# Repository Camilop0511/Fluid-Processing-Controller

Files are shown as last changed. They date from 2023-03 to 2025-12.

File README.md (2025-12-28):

# Fluid Processing Controller 

## Overview 
This project implements a Fluid Processing Controller designed to simulate a small-scale industrial process, focusing on real-time monitoring, sequential control, and hardware–software integration. The system involves acquiring and controlling process variables related to fluids. It uses electronic components for fluid level and temperature measurements, including an MPX2010 pressure sensor for precise liquid level detection and an LM35DZ temperature sensor for accurate temperature monitoring.

The system features two storage tanks and a processing tank, managed by two water pumps and a heating resistor. It has both a physical control panel and a web-based interface for control. An ATmega8515 serves as the main controller, facilitating bidirectional communication with a Raspberry Pi. This setup allows users to input parameters and monitor the process through a web page hosted by the Raspberry Pi. 

Operationally, the system functions sequentially, ensuring meticulous control over each stage of fluid processing. This includes tasks such as filling, heating, and final delivery of the processed fluid.

## Repository Structure
- `src/`: Final version of the code.
- `test/`: Contains development history.
  - `microcontroller/`: Experimental and development code with test folders for various functionalities.
    - `actuators/`: Test code related to actuators.
    - `pwm/`: Test code for Pulse Width Modulation.
    - `sensors/`: Test code for sensors.
    - `sequential_control/`: Sequential control tests.
    - `serial_communication/`: Code test for serial communication between the microcontroller and Raspberry Pi.
  - `web_server/`: Development history of the web server code.
- `docs/`: Documentation files such as circuit designs, PCB designs, PCB illustrations, and a technical manual.

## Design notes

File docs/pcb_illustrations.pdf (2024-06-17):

243-698-DW Computer Network Project | 1

# 243-698-DW Computer Network Project

# PCB Illustrations

# Camilo Loaiza

1835111

# Nick Markou

# 28 April 2023

## Table of Contents

## 1. Main PCB Design

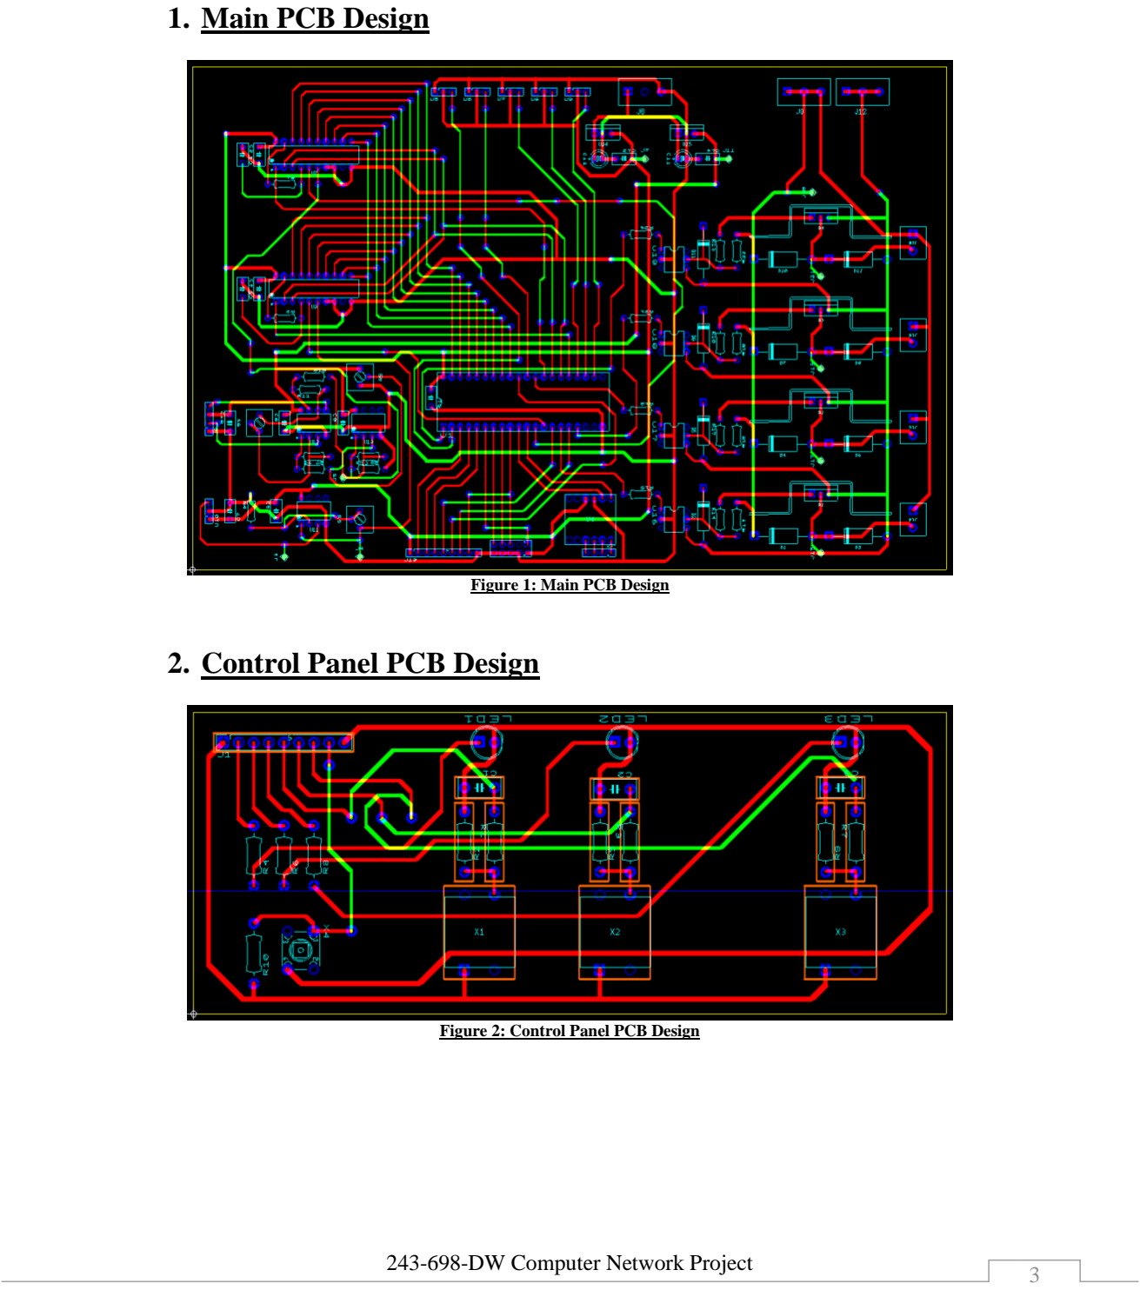
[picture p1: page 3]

Figure 1: Main PCB Design

## 2. Control Panel PCB Design

Figure 2: Control Panel PCB Design

## 3. Main PCB Layout

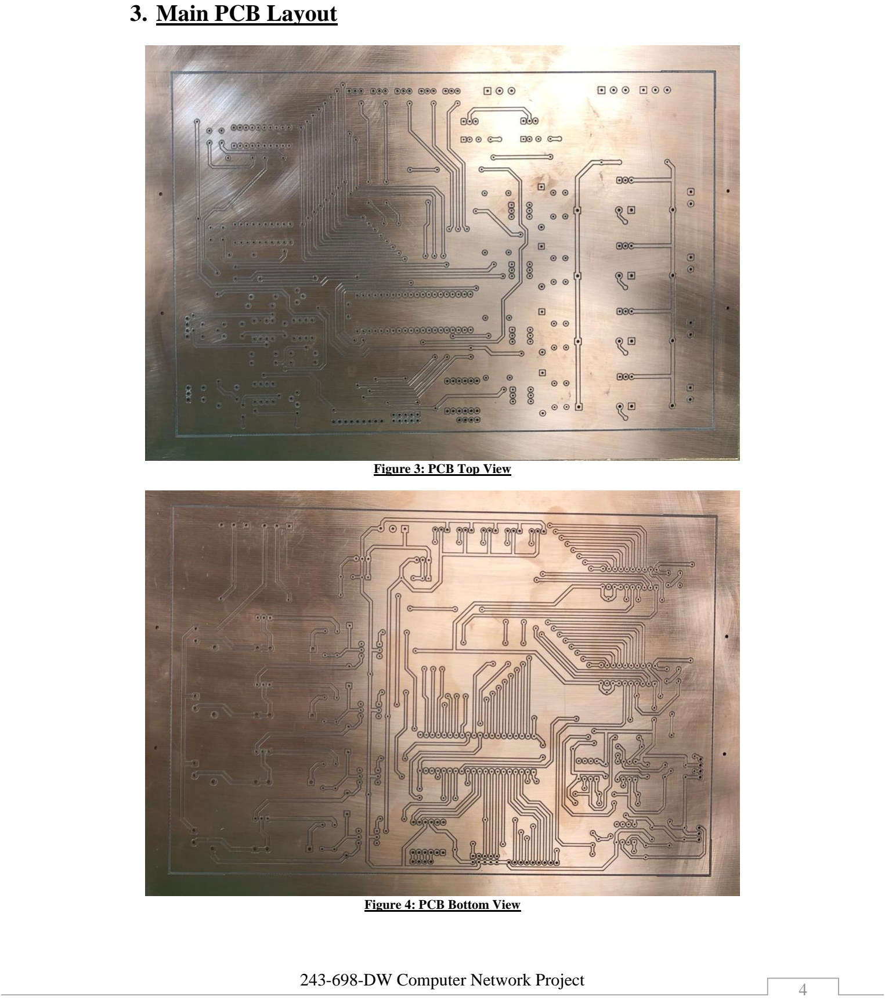
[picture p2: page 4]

Figure 3: PCB Top View

Figure 4: PCB Bottom View

## 4. Main PCB Vias Soldering

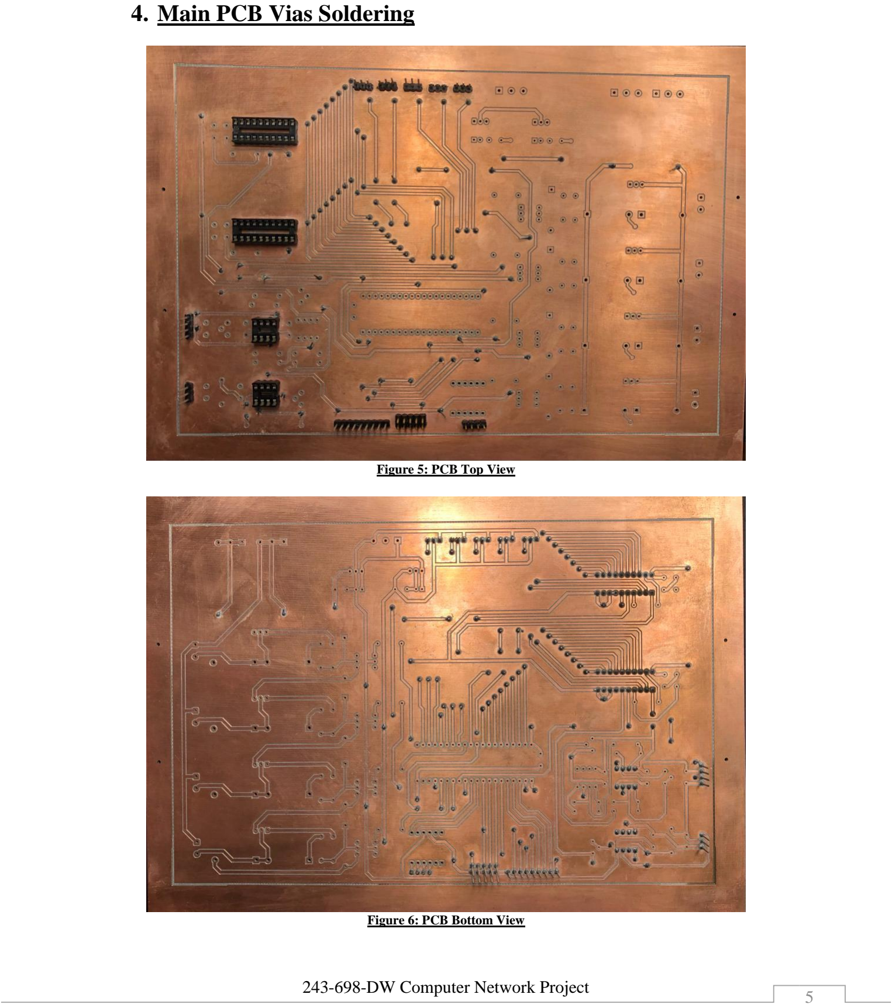
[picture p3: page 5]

Figure 5: PCB Top View

Figure 6: PCB Bottom View

## 5. Main PCB Soldering

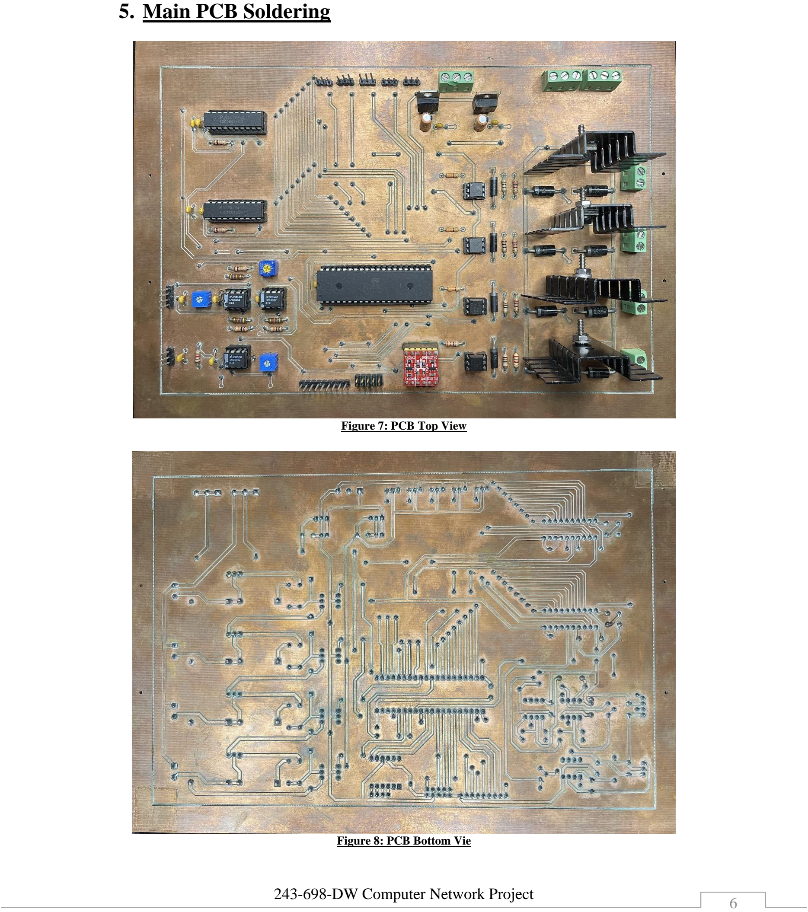
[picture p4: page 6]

Figure 7: PCB Top View

Figure 8: PCB Bottom Vie

## 6. Control Panel PCB Layout

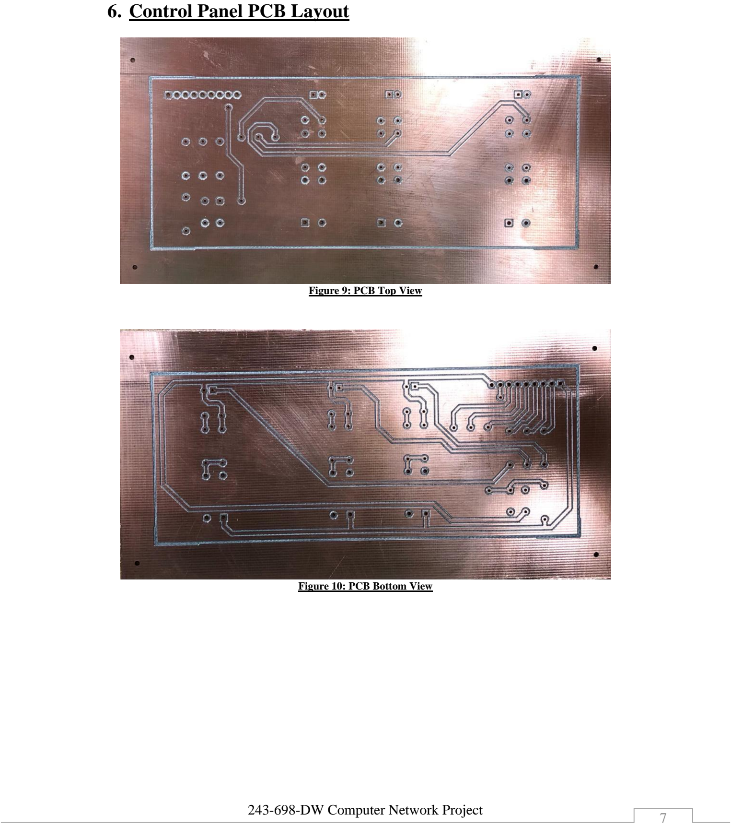
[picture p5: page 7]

Figure 9: PCB Top View

Figure 10: PCB Bottom View

## 7. Control Panel PCB Soldering

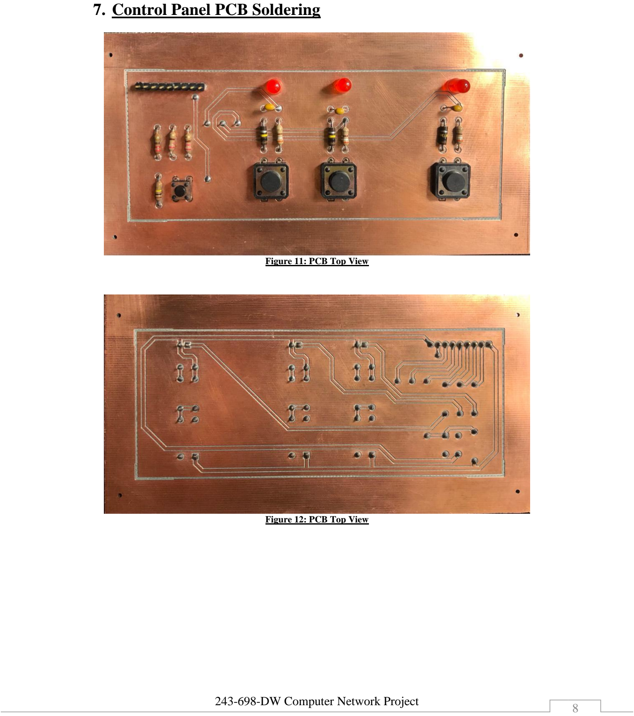
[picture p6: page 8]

Figure 11: PCB Top View

Figure 12: PCB Top View

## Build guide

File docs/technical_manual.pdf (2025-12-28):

## Table of Contents

## User Guide

## 1.0 Introduction

The resulting product of this project is a fluid processing controller that emulates a small-scale industrial process. It involves the acquisition and control of process variables with fluids using basic components for fluid level and temperature measurement such as pressure and temperature sensors. The system includes two liquid storages, a processing tank, and both physical and virtual control panels. Additionally, two water pumps are used to control the level in the processing tank coming from the storage tanks, a heating resistor is used to warm the water to the temperature that the user sets and an electro valve is utilized to serve the liquid when the process is finished. The genesis of this project is my interest in the food manufacturing industry and my desire to eventually have my own food processing business.

## 2.0 Setup and Operation

To properly configure and operate this product, it is necessary to connect both 12V and 24V power supplies to the PCB, as well as the temperature and pressure sensors and all actuators to their corresponding headers on the PCB. The Raspberry Pi must be powered on and its serial ports connected to the PCB, while also ensuring it has internet connectivity. To begin the process, the user should navigate to the Raspberry Pi's IP address, which can vary depending on the network's DHCP settings, and access the form page at /fluids_project/web_server/form.html. For example,
if the | Raspberry | Pi's | IP | address | is | 10.0.0.83, | the | user | should | browse | to
http://10.0.0.83:8080/fluids_project/web_server/form.html. On the form page, the user can enter their desired settings for the process, taking note of the restrictions and limits set for the parameters to optimize the system. Once the user has submitted the form, they can start, stop, and monitor variables such as temperature, processing tank volume, the state of start, stop and serve, as well as the current step of the process being executed. These are the different steps of the system and their meaning:
- Step 0: Microcontroller is waiting for serial values from Raspberry Pi.
- Step 1: The values sent from the Raspberry Pi are transferred to process variables.
- Step 2: Water Pump 1 is started.
- Step 3: Water Pump 1 is stopped.
- Step 4: Water Pump 2 is started.
- Step 5: Water Pump 2 is stopped.
- Step 6: Heating resistance is started.
- Step 7: Heating resistance is stopped.
- Step 8: Cooldown counter is executed.
- Step 9: Liquid can be served (electro-valve is opened).
- Step 10: Electro-valve is closed.

## 3.0 Specifications

Parameter | Minimum | Maximum | Unit
Input Voltage (Control circuit) | | 5
circuit) | | 24 | V Input Voltage (Power
Storage Tank Volume | | 1300 | ml
Water Pumps Voltage | 6.3 | 16.8 | V
Water Pumps Current | 0.27 | 0.83 | I
Water Pumps Power | 1.7 | 14 | W
Temperature in Processing Tank | 10 | 60
Temperature | 23 | 30 | °C Heated Liquid
Heating Resistor Voltage | 4.65 | 22.9 | V
Heating Resistor Current | 0.18 | 0.82 | I
Heating Resistor Power | 0.84 | 18.78 | W

## Technical Guide

## 4.0 System Diagram

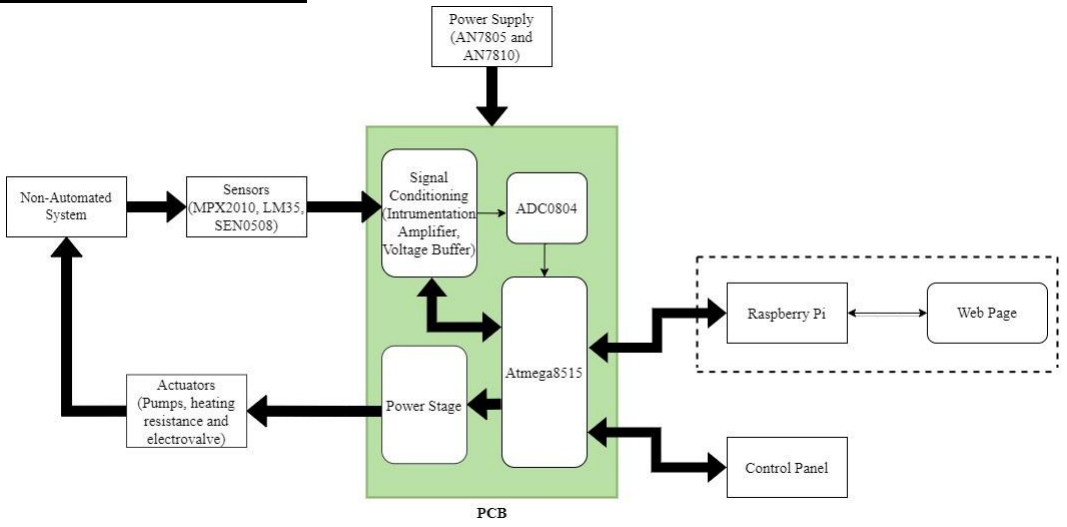
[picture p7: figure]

## 5.0 System Description

- Sensor Module:
- Pressure Sensor: The purpose of the MPX2010 pressure is to provide precise and reliable detection of the liquid level in the processing tank. This sensor works by measuring the pressure difference between its two ports, one exposed to the atmosphere and the other one exposed to the liquid in the tank, which changes the electrical resistance of the sensor as the liquid level changes. The intended operation is to ensure that the liquid level remains within the intended optimal ranges, while enabling accurate monitoring of the processing operation.
- Temperature Sensor: The purpose of the LM35DZ waterproof temperature sensor is to accurately measure and monitor the temperature of the liquid in the processing tank, and convert it into the corresponding electrical signal. The sensor’s output is linear, and proportional to the temperature in Celsius, with a scale factor of 10mV/ °C, which allows accurate and reliable temperature monitoring, and ensures that the processing tank operates within the desired temperature range.
- Capacitive Sensors: This module is designed to detect liquid level in the tanks using SEN0506 capacitive sensors. The purpose of this module is to determine whether the liquid level in the storage tanks is high or low, while in the processing tank, it will detect only the high level. The capacitive sensor used in the processing tank is as used as a redundancy method, since it works alongside the pressure sensor guaranteeing that the high liquid level in the processing tank is always detected and providing an extra layer of protection.
- Signal Conditioning Module:
- MPX2010 Signal Conditioning: The purpose of the signal conditioning module is to prepare the voltage signal obtained by the MPX2010 pressure sensor for use with the Analog-to-Digital converter. To achieve this, two LMC6062 OP-AMPs are connected to the sensor to server as an instrumentation amplifier. The instrumentation amplifier allows to filter out any noise present in the signal, adjust the offset, and adjust the gain before the signal is connected to the A/D converter. The intended operation is to ensure that the signal is optimized for the best possible measurement accuracy, and to minimize signal distortion.
- LM35 Signal Conditioning: The signal conditioning module for the LM35DZ temperature sensor prepares the analog signal for conversion into digital form by the ADC. Its purpose is to ensure accurate temperature readings by amplifying the signal, performing calibration, and linearization. By incorporating a gain of 5, this module enhances the signal’s sensitivity for better resolution and sensitivity. This module plays an important role to maintain the quality and consistency of the processing tank operation.
- ADC0804 Module: The purpose of the ADC0804 module is to convert the amplified analog voltage signal obtained from the instrumentation amplifier into digital format that can be read and processed by the Atmega8515 microcontroller. In addition to the pressure sensor’s ADC, another ADC0804 integrated circuit has been added to handle the analogto-digital conversion of the LM35DZ temperature sensor. The purpose of this module is to convert the voltage signal from the LM35DZ temperature sensor, which has already been amplified by the signal conditioning module, and the liquid level in the processing tank into digital data that can be processed by the microcontroller, providing accurate and reliable temperature and liquid level data for monitoring the processing tank operation. This module’s intended operation is to sample and convert the analog temperature signals and liquid level into digital data when indicated by the program.
- Power Supply Module: The power supply module comprises two regulated power supplies. The first is a 12V DC plug power supply adaptor that serves as the input to an LM7810 regulator, which supplies a stable 10V to the instrumentation amplifier. The same 12VDC plug also serves as the input to an LM7805 regulator, which provides a reliable 5V supply for the microcontroller, ADC, LM35 temperature sensor, and its signal conditioning module, a voltage buffer based on an operational amplifier. Additionally, a DC 24V 10A Power Supply Adapter Transformer Regulated Switch is utilized to power the actuators, which include the two water pumps, heating resistance, and electro valve. The power supply module not only provides the necessary voltage to operate all modules but also ensures the separation of the control and power sections of the circuit for enhanced safety. This separation is important given that the control section operates with 5V while the power section requires 24V.
- Power Stage Module: The power stage module is composed of four circuits, each dedicated to one of the four high-power actuators, all powered by 24V. The purpose of this module is to control the actuators’ power supply safely and efficiently using lower-power signals from the Atmega8515 microcontroller. To achieve this, optocouplers are used to isolate the high-voltage actuators from the low-voltage microcontroller, preventing voltage spikes and protecting the microcontroller, and allowing safe and efficient control of the power supply. The MOSFETs act as electronic switches that regulate the current flow to the actuators. The operation of the chopper circuit is synchronized with the microcontroller's PWM output signal, which serves as the input to the optocoupler and regulates the gate voltage of the MOSFETs. The chopper circuits use this switching mechanism to efficiently regulate the actuators' power supply while ensuring their safe operation and providing reliable control of the actuators.
- Actuators Module:
- Water Pumps: The purpose of the two water pumps is to transfer liquid from the storage tanks to the processing tank through pipelines. This transfer process is accomplished by regulating the speed of the water pumps through the chopper circuit, which is controlled by the Atmega8515 microcontroller's PWM signal. The intended operation of the water pumps is to accurately adjust their speed according to the signal received from the power stage module ensuring a precise liquid transfer.
- Heating Resistance: The heating resistance is responsible for raising the temperature of the processing tank’s liquid to a programmed value by converting electrical energy into thermal energy. The Atmega8515 microcontroller sends a PWM signal to the power stage module, which then controls the power delivered to the heating resistance. Overall, the intended operation of the heating resistance is to provide precise control of the liquid temperature through the microcontroller’s PWM signal and the power stage module.
- Electro valve: The electro valve serves as a security feature that prevents liquid from being served until the entire process is complete, and the user-defined cooling time has elapsed. The microcontroller controls the electro valve, allowing it to operate in two states: ON or OFF. If the conditions are not met, the electro valve remains OFF. The electro valve is connected to a regular port on the microcontroller since it only has two states, and also passes through the power stage module. Overall, the intended operation of the electro valve is to provide an added layer of safety and control to the processing tank’s liquid flow.
- The Atmega8515 Module: This module serves multiple purposes in the system. First, it is responsible for processing digital data obtained from the ADC0804 module, more specifically from the pressure and temperature sensors, which are passed through the signal conditioning and ADC modules. Additionally, This module also controls the actuators with the help of three PWMs which are configured on the microcontroller: two 16-bit PWMs which serve the two water pumps, and one 8-bit PWM that controls the heating resistance. The signals are sent to the power stage module, which then controls the actuators. Another of its responsibilities is the sequential control of the system. The sequential control involves a series of steps that must be followed to complete the processed, as long as all the necessary conditions are met. If any of the conditions in the step is not met, the process will not proceed to the next step. This sequential process is comprised of 11 steps:
- Step 1: The microcontroller waits for the process values from the Raspberry Pi, as well as the start signal.
- Step 2: The serial communication variables are transferred to the process variables.
- Step 3: Water pump 1 is started with the user-defined value.
- Step 4: Water pump 1 is stopped.
- Step 5: Water pump 2 is started with the user-defined value. o Step 6: Water pump 2 is stopped. o Step 7: The heating resistance is started with the user-defined value.
- Step 8: The heating resistance is stopped. o Step 9: The cooldown time counter is executed. o Step 10: Liquid is served after the serve signal is sent by user (electro-valve is opened). o Step 11: Electro-valve is closed after the pressure sensor detects that the water level is low.

The control sequence is dependent on meeting the necessary conditions and status of the start and stop signals. If the user sends a stop signal on the web server or physical control panel, the process will stop until a start signal is sent. The process then restarts from the step where it was stopped. Additionally, the process checks the water level of the storage tanks. If an empty tank is detected, or an error with the storage tank sensors is identified, the process will also stop.

The microcontroller is also responsible for the two-way serial communication with the Raspberry Pi. It reads two bytes sent by the Raspberry Pi to obtain the initial user-defined process values, where the first byte corresponds to a command identifying the type of data being sent, and the second byte is the data value. The same principle is applied when sending data from the microcontroller to the Raspberry Pi. The data values sent include the step, temperature, volume, start signal state, stop signal state, serve signal state and cooldown counter state.

- Raspberry Pi: The Raspberry Pi module serves two main purposes, which are hosting the web page, and communicating with the Atmega8515 microcontroller.
- Web Page: The web page is hosted using Apache 2 to provide a web server that allows direct interaction with the user. The main page, called form.html, prompts the user for multiple parameters that define the system’s behaviour, including the percentage of liquid from each tank, the speed of the water pumps, the desired temperature, the power percentage for the heating resistors, and the desired cooldown time before serving the liquid. The data from this page is then submitted to the formresults.php file, which comprises HTML, PHP, and JavaScript code. This page handles all the backend server process that is needed to effectively communicate with the Atmega8515 microcontroller.
- Logic Level Converter: This module facilitates the communication between the Atmega8515 microcontroller and the Raspberry Pi. This is achieved by converting the different voltage signals between the 3.3V logic level of the Raspberry Pi and the 5V logic level of the Atmega8515.
- Control Panel: The control panel module serves as a physical redundancy element for the buttons on the web page, enabling control over the system’s sequential steps by sending start, stop, and serve signals, just like the web page buttons. The control panel has the same functionality as the web page buttons but it offers added flexibility. In case of a web crash, unavailable internet connection, or failure to send data, the control panel allows for continued control over the system, enabling it to be stopped if necessary, and started without needing to use the web page. Additionally, the control panel includes three LEDs:
start, stop, and serve, which indicate the current status of the industrial process.
- PCB: The purpose of the PCB (Printed Circuit Board) is to provide a reliable connection for the multiple electronic components, including the microcontroller, ADCs, sensors, MOSFETs, actuators, and all other devices. The main PCB is divided into two parts: the control section on the left, which is comprised of the microcontroller and low-power devices, and the power section on the right, which is composed of the 24V-powered devices that provide control over the actuators. These two sections are separated by optocouplers that provide both electrical and visual isolation. The second PCB is the control panel which comprises the buttons and LEDs, and it is connected to main PCB using headers and wires.
- Non-automated Module: This module consists of various components that are part of the system but do not belong to the electrical circuitry such as the structure, the liquid storage tanks, the processing tank, and pipelines. One port of the MPX2010 pressure sensor is connected to a tube that is taped to the bottom of the processing tank to measure the pressure level of the liquid in the tank. ¼ inch vinyl tubing is being used to measure the pressure in the processing tank. The processing tank, along with two 4L storage tanks and pipelines, are also included in this module. The water pumps are connected to the storage tanks and the processing tank via 1/2 inch vinyl tubing, while the processing tank is connected to the electro valve using 3/8 inch vinyl tubing Additionally, manual valves were added to the processing tank to optimize the liquid’s flow and to act as redundancy components.

## 6.0 Circuit Description

- System’s Circuit

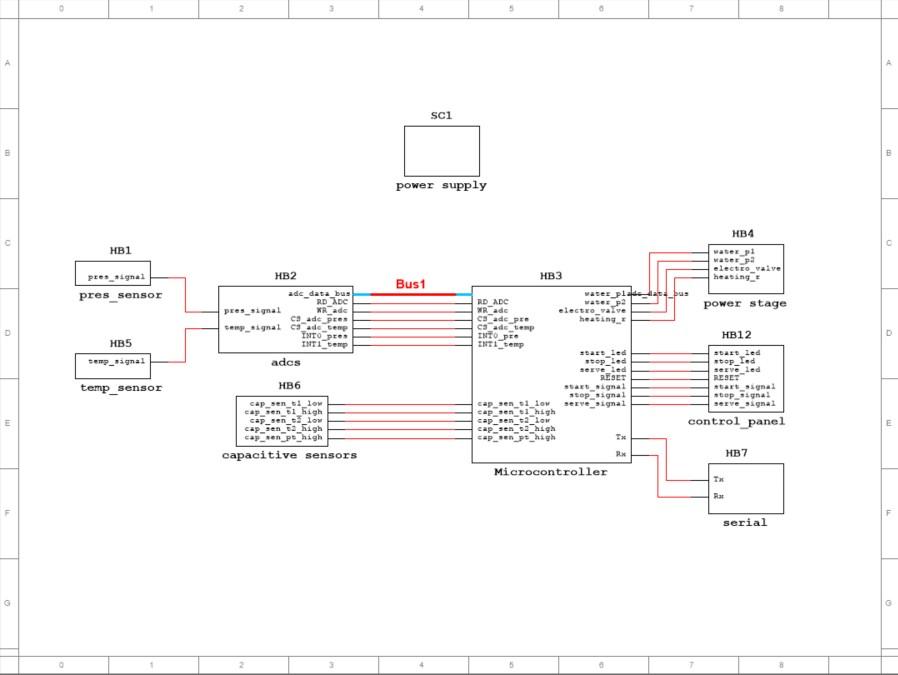
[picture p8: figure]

- Microcontroller: The control panel is connected to the microcontroller using regular ports configured as input for the start and serve signals, and as output for the LED signals. However, the stop button is connected to INT2 since it is a signal that requires immediate execution in the code and cannot be executed using the polling method. The logic level converter is connected to the Rx and Tx pins on the ATmega8515 which are part of the USART interface. The ADCs are connected to the address port, the control signals are connected to regular ports, and the ADC interrupts are connected to the interrupts on the microcontroller. The actuators are connected to the PWM pins, except for the electro-valve which is using a regular port.

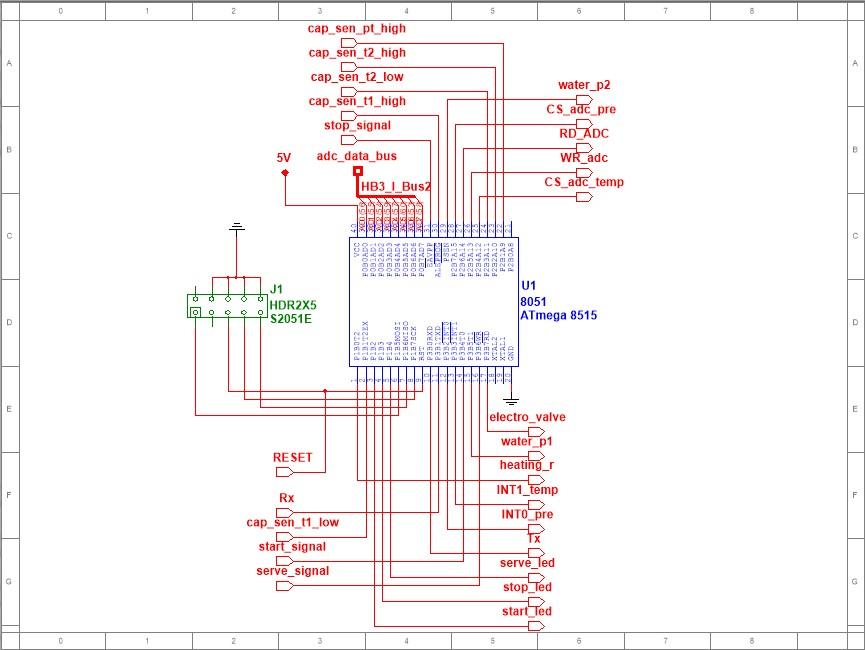
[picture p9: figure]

- ADCs: The data buses of both ADCs are connected to the same Port A of the Atmega8515 microcontroller, enabling the microcontroller to read data from each ADC. The write (/WR) and read (/RD) signals of both ADCs are also connected to the same /RD and /WR pins of the microcontroller, allowing the microcontroller to have control over their operation. The Chip Select (/CS) signal of each ADC is connected to different ports on the microcontroller, enabling the microcontroller to select which ADC to communicate with and read data from. The two ADCs are configured to run as interrupt-driven, meaning that when an ADC completes a conversion, it generates an interrupt signal on its INT pin which are connected to the microcontroller’s INT0 and INT1 external interrupts. The temperature and pressure sensors’ signals are connected to the inputs of the two ADCs, after passing through the signal conditional circuits, which are converted into digital values.

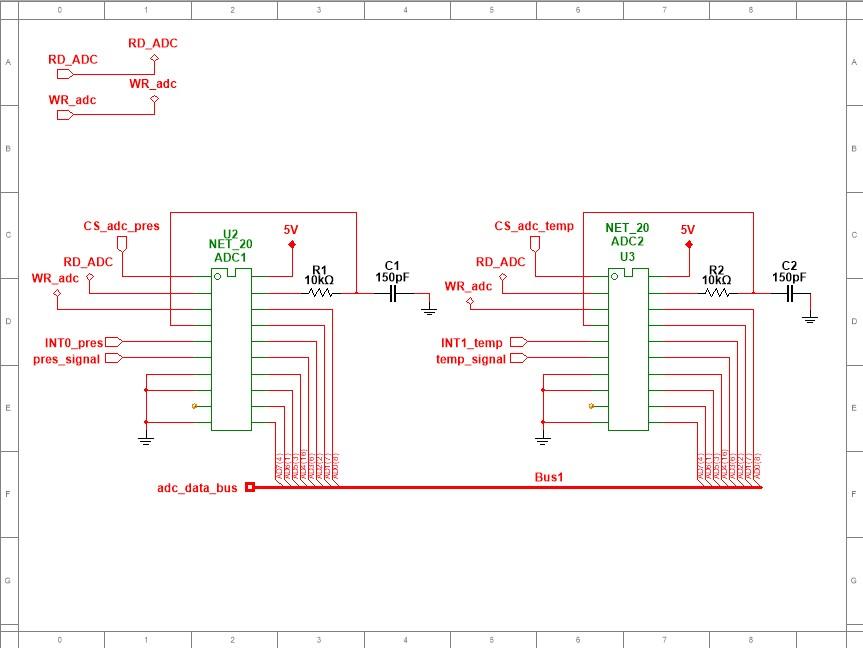
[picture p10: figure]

- Serial/Logic Level Converter: The logic converter is divided into two parts: the upper part connects to the Rx and Tx pins of the microcontroller and is also connected to is 5V VCC and ground, while the bottom part connects directly to the Rx and Tx pins of the Raspberry Pi, and to 3.3V and ground. This configuration ensures that the signals are properly converted between the two different voltage levels (5V and 3.3V) facilitating the exchange of data between the AVR microcontroller and the Raspberry Pi.

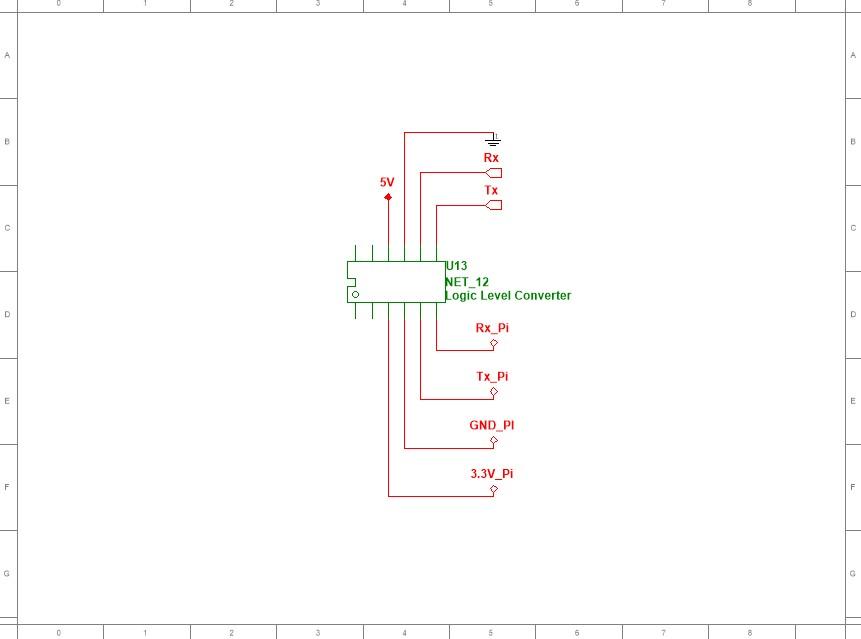
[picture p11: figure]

- Capacitive Sensors

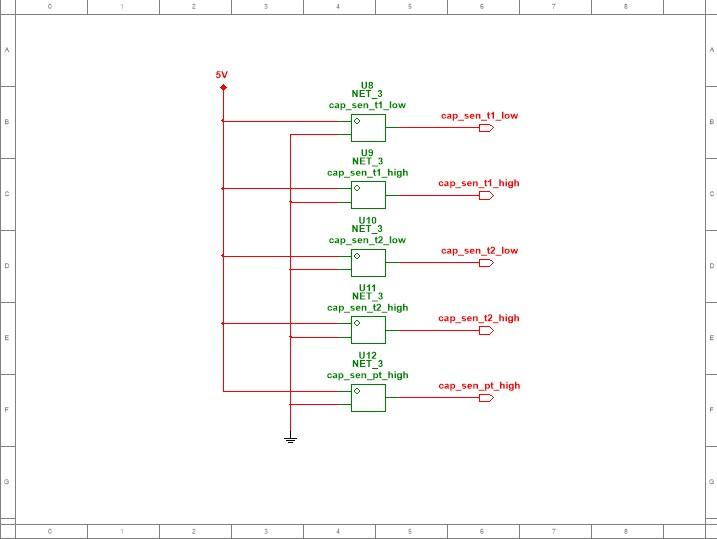
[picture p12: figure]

- Power Stage: The power stage circuit is designed as a chopper circuit. The PWM signal from the microcontroller is connected to the internal LED of the optocoupler. The ground of this LED is the same as the control section of the system. The transistor inside the optocoupler is connected such that the emitter is connected to the ground of the power section and the collector is connected to a resistor that goes to VCC (24V). A 1N5349 Zener diode connected between these two pins to act as a 12V voltage regulator to protect the MOSFET. The gate of the MOSFET is connected to the collector of the internal transistor of the optocoupler. Two 1n5401 diodes are connected to the MOSFET, one in parallel with the MOSFET having the cathode of the diode to the drain of the MOSFET and the anode to the source, and the other going from the drain to VCC in parallel with the load. These diodes protect the MOSFET and load from damage by preventing current from flowing back to them.

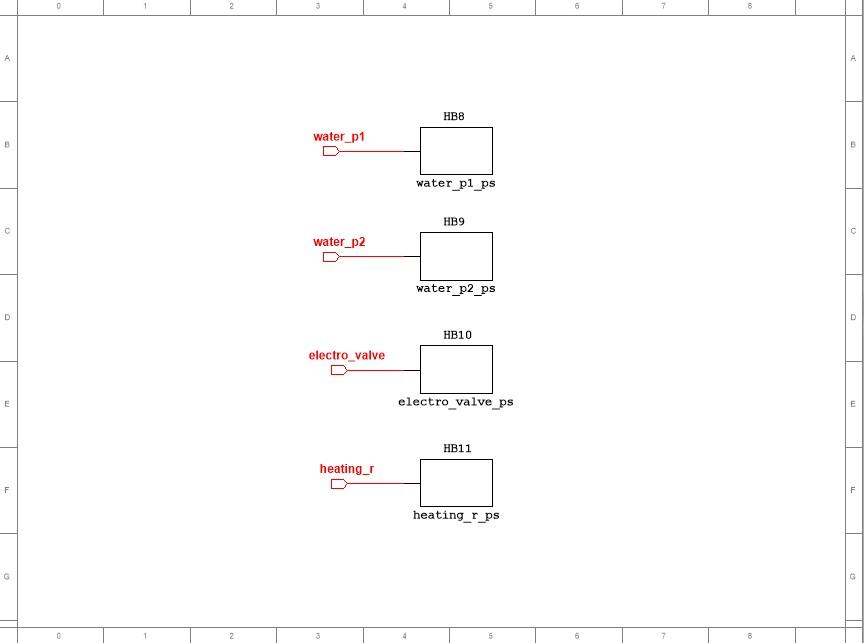
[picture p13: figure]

- Water Pump 1 Power Stage:

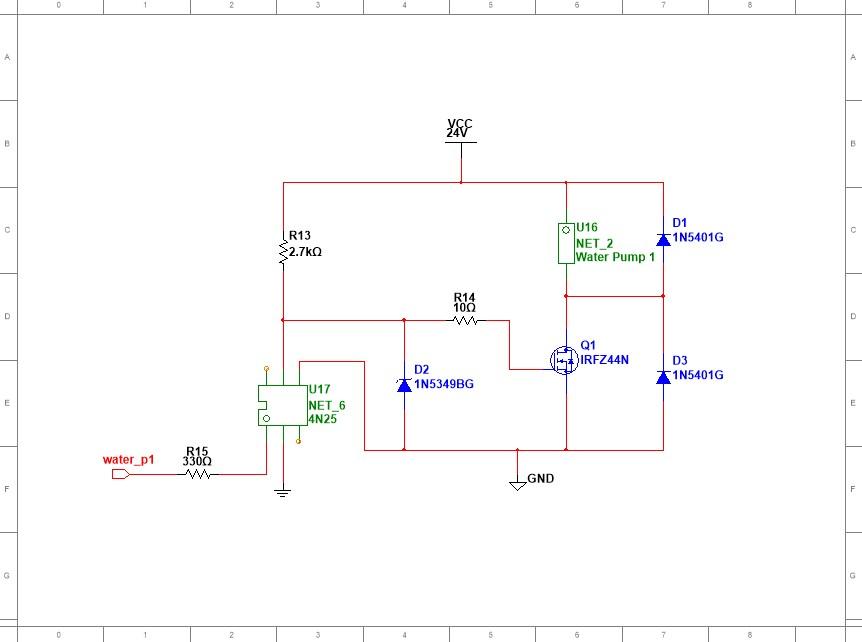
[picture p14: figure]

- Temperature Sensor: The LM35DZ signal conditioning circuit conditions the output of the LM35DZ sensor using an operational amplifier voltage buffer configuration. The noninverting input of the LMC6062 op-amp is connected to the output of the LM35DZ sensor, while the inverting input is connected to a 1k ohms resistor that is grounded. The loopback resistors of the circuit is a 5k ohm potentiometer that allows the gain of the circuit to be adjusted. This circuit has a gain of 5, meaning that if the output of the temperature sensor if 0.25V, the output of the circuit will be 1.25V.

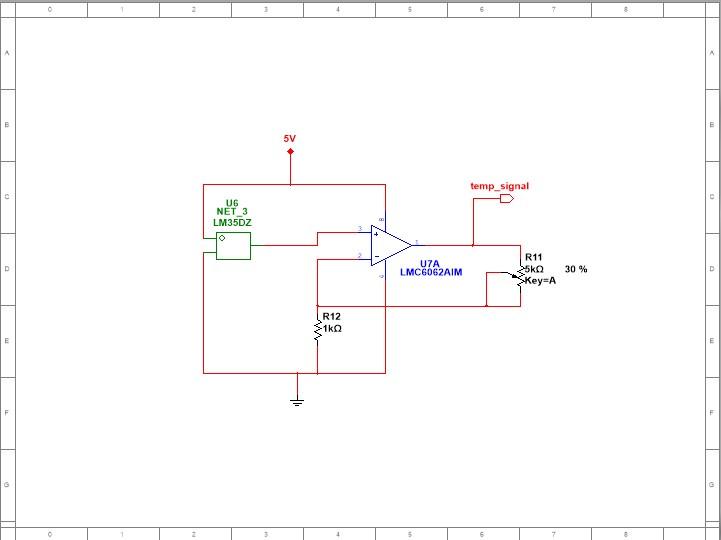
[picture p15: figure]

- Pressure Sensor: Three OP-AMPs are use to amplify the signal of the MPX2010 pressure sensor. The sensor’s differential outputs are connected to the input of two different OPAMPS and their outputs are connected to the inputs of the other OP-AMP. The outputs of the sensors are connected to pin 2 and 5 of the instrumentation amplifier, with feedback resistors set at 47k ohms, and a gain resistor of 1k ohms. The offset resistor is 20k ohms, and the output of the instrumentation amplifier (pin 1 of the third op-amp) is connected to the voltage input of the ADC.

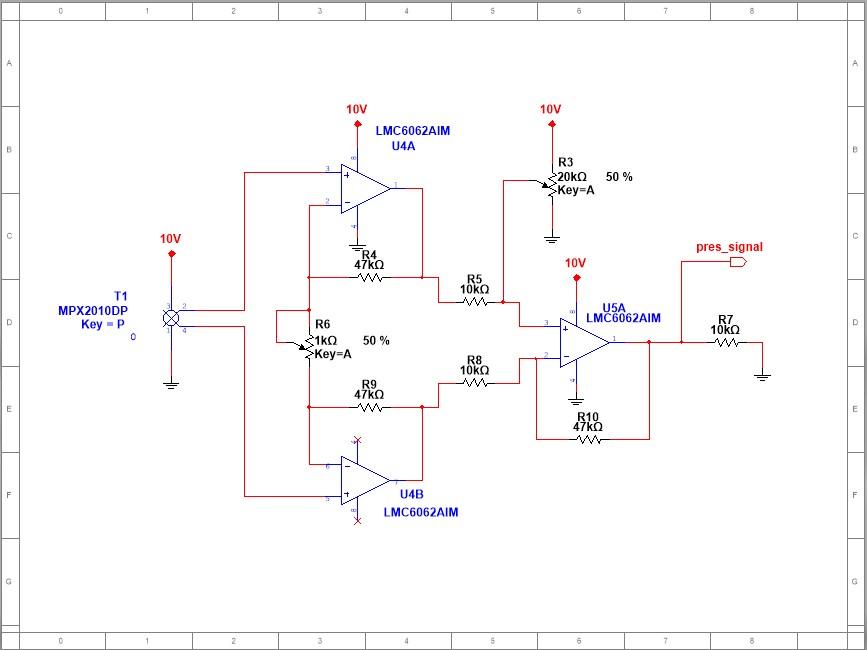
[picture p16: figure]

- Power Supply: The power supply circuit consists of two voltage regulators: LM7805 and LM7810, both of which are connected to the 12V output of the DC plug power supply adapter. A 0.33uF capacitor is connected between ground and input voltage, and a 0.1uF capacitor is connected between ground and output voltage for the 5V regulator, which supplies power to the microcontroller, ADC, LM35 temperature sensor, and op-amp voltage buffer. These capacitors help to filter out noise and ensure stable voltage output. The same configuration is used for the 10V regulator which is supplies power to the pressure sensor and the instrumentation amplifier. This circuit is designed to provide stable and regulated power to the various components of the system avoiding damage from voltage fluctuations.

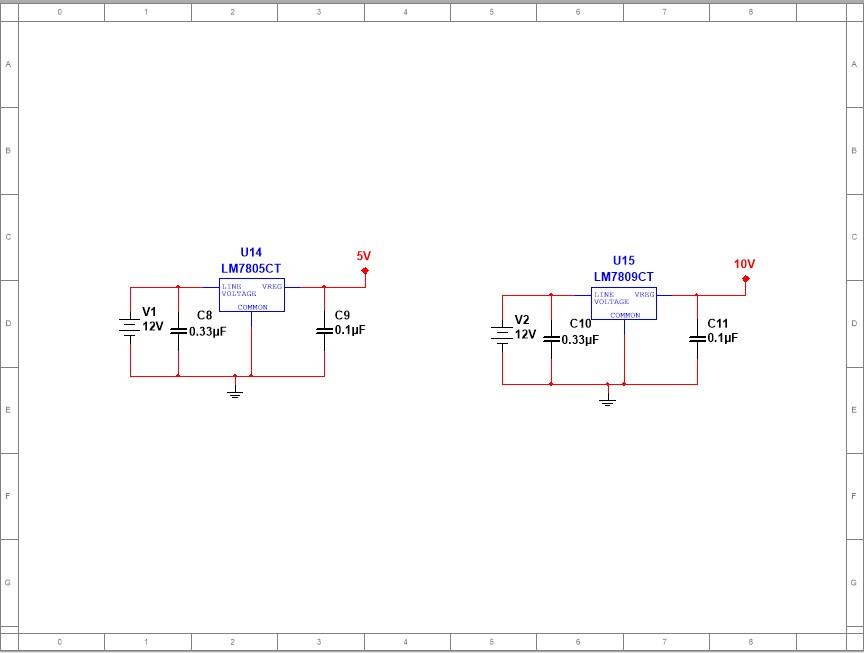
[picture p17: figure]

- Control Panel: The control panel consists of three push-buttons and three LEDs. The LEDs are configured with a simple circuit consisting of an LED and a 220 ohms resistor, which limits the current. The signals that turn the LEDS ON and OFF come directly from pins PB2, PB4, and PB4, for the start, stop and server signals respectively which are all configured as output ports. The circuit configuration for the push buttons includes a pushbutton, a 100k resistor to limit the current and protect against overvoltage, and a low-pass filter consisting of a 390 ohm resistor and a 100nF capacitor. This low-pass filter prevents switch bouncing by avoiding multiple transitions from happening during switch closure, which in return provides a cleaner signal.

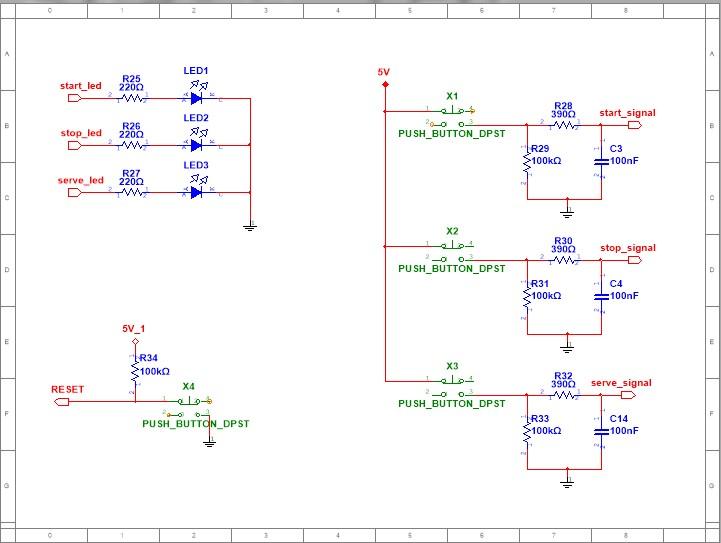
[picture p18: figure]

## 7.0 Software Description

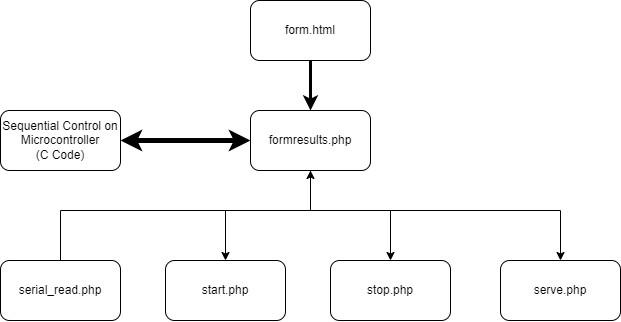
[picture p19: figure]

- Sequential Control: This code reads data from the two sensors via the ADCs. This code initializes the USART communication and sets up the control pins for the two ADCs. The ADCs are controlled by four control pins, and two external interrupts that are used to trigger when the data from the ADCs is available. When the code selects the appropriate /CS of the ADC, the microcontroller waits for the interrupt signal, reads the data, and deselects the sensor. After the data is collected, the temperature value is calculated, converted to Celsius. The pressure data is also calculated to obtain the level of the processing tank in millimeters which will be eventually converted to volume on the Raspberry Pi. The code also controls the water pumps, the heating resistor through pulse width modulation (PWM) signals based on the percentage input received via USART communication. The code receives input from USAR converts the numeric value to percentage for the PWMs duty cycle, and sets the respective PWM signal. Furthermore, to combine the sensors and actuators to work together, a sequential control has been implemented on this code based on the stop and start signals, and the state of the sensors and actuators. Each step represents a particular task in the operation of the system that involves both the sensors and actuators. The system waits for the user input or sensor values to advance to the next step. This system uses the Rx interrupt function to read incoming bytes whenever new data is received on the USART interface. The commands that used in the first byte are hexadecimal codes that represent the different types of data, the second byte represents the data being received. These commands are predefined so that the microcontroller and the Raspberry Pi can interpret the data correctly. These are the commands that are being used to read serial data on the Microcontroller:
- 0x5B: Water pump 1 received speed data
- 0x4A: Tank 1 volume data
- 0x3D: Water pump 2 received speed data
- 0x2C: Tank 2 volume data

- 0x1F: Liquid's temperature data
- 0x4E: Heating resistance power data
- 0x0E: Cooldown timer data
- 0x0A: Start signal
- 0x5F: Stop signal
- 0x1B: Serve signal
- form.html: This HTML code defines the parameters for the system. It has multiple input fields that are supplied by the user, including one for liquid percentage from each storage tank, two for water pump speeds, one for the temperature, one for the heating resistor power, and one for cool-down time. This code also uses a JavaScript function that checks if the sum of the two inputs for the liquid percentage parameters is less than 90%, and alerts the user if the value is higher than this limit. All the inputs are required, and the ranges are checked using parameters. This form submits to the formresults.php PHP file.
- serial_read.php: This PHP script reads data from the serial port sent by the microcontroller. It reads one byte at a time looking for a command byte, and uses a switch statement to process the byte according to its value. Depending on the value of the command, the script assign different values to the variables. The script stores the received data into an array and returns it the formresults.php file as JSON. These are the command values being used to read values from the microcontroller:
- 0xA3: Step o 0xB4: Temperature
- 0xC5: Volume
- 0xD1: Start state
- 0xE2: Stop state
- 0xF6: Serve state
- 0x9A: Cooldown counter
- start.php, stop.php, serve.php: These scripts transmit the start, stop, and serve signals to the microcontroller via serial communication using the 0x0A, 0x4A, 0x1B bytes respectively, followed by the data values.

## 8.0 Testing and Calibration

- Testing:
- Sensors Code: These are the values obtained by the ADCs, the 0xFF value indicates that the processing tank has reached maximum capacity as determined by the pressure sensor. Additionally, the temperature sensor’s converted value is represented by in Celsius, which is equivalent to 26 in decimal, and since this test was done at room temperature, this outcome reflects the effectiveness of the conversion process and proves that the temperature sensor and its corresponding code are operating as expected.

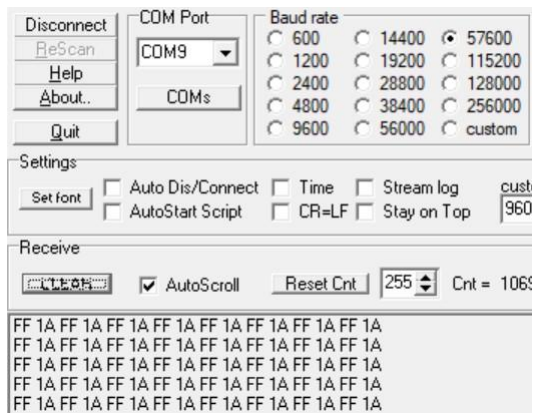
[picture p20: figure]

- Actuators: Due to the chopper circuit configuration, the PWM signal has to be inverted to function properly, meaning that the duty cycle seen by the load is 30%. The signal of the first probe is the input of the optocoupler, and since the circuit was being tested, a signal generator was used to simulate the PWM. The signal on the second probe is the output of the chopper circuit, and it can be observed that the MOSFET is working as expected having an output of 24V, and modulating the same square wave as the optocoupler’s input signal.

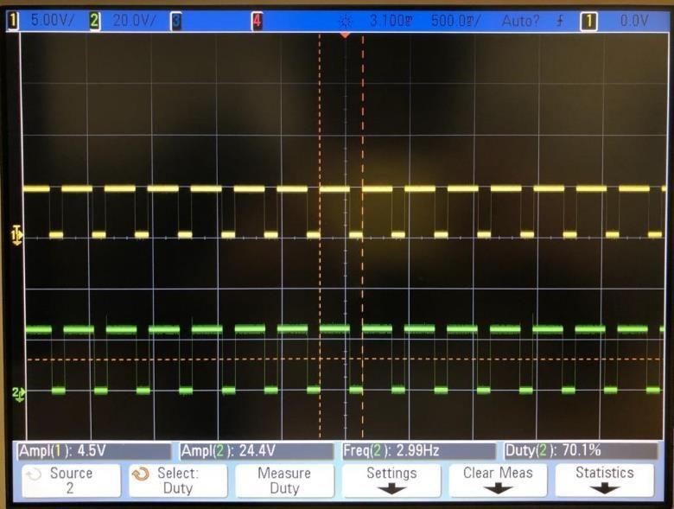
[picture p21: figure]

- Water pumps: The following table shows the performance of the water pumps under different duty cycle percentages:
Duty Cycle % | Current (A) | Voltage (V) | Power (W)
10 | 0.07 | 1.1 | 0.077
20 | 0.25 | 3.7 | 0.93
30 | 0.27 | 6.3 | 1.7
40 | 0.32 | 8.6 | 2.75
50 | 0.47 | 11 | 5.17
60 | 0.62 | 13.3 | 8.25
70 | 0.76 | 15.6 | 11.86
80 | 0.9 | 18 | 16.2
90 | 1.08 | 21 | 22.69
100 | 1.17 | 23.6 | 27.6
- Heating Resistance: The following table shows the performance of the heating resistance under different duty cycle percentages:
Duty Cycle % | Current (A) | Voltage (V) | Power (W)
10 | 0.07 | 1.94 | 0.14
20 | 0.18 | 4.65 | 0.84
30 | 0.26 | 6.94 | 1.80
40 | 0.34 | 9.20 | 3.13
50 | 0.42 | 11.46 | 4.81
60 | 0.50 | 13.74 | 6.87
70 | 0.58 | 16.03 | 9.30
80 | 0.66 | 18.33 | 12.10
90 | 0.76 | 21.30 | 16.19
100 | 0.82 | 22.9 | 18.78

- 2-byte configuration being sent by the web server: These are test examples of how the microcontroller receives the data values. I had my PC connected as a “spy” to be able to see the values being sent by the microcontroller. As we can see in the second example, the Water pump 1speed percentage is 80% (I had made a mistake when I took this screenshot and put percentage of liquid in the html file instead of water pump 1 speed percentage), and the command corresponding to water pump 1 speed percentage is 0x5B, and 80 in hexadecimal is 0x50, which corresponds to “[P” in ascii

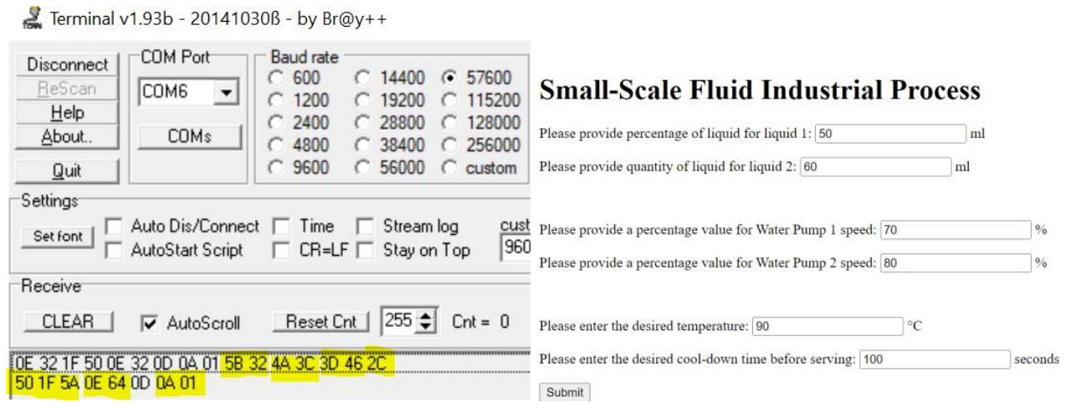
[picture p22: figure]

- Sequential Control:
- Step 0: The microcontroller is waiting for the values from the web server. We can see that the volume of the tank is less than 100ml. and the status of the start button is 0.

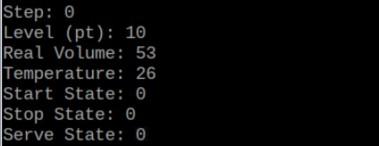
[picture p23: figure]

- Step 1 and 2 : The web server sends all the parameters values and the start signal, and since the processing tank is has less than 100ml, it goes directly to step 2. In
step 2, water pump 1 starts. The maximum volume of the processing tank is 1300ml, and since the parameter value for the percentage liquid from storage tank 1 is 50%, water pump 1 will be ON until the pressure sensor detects that the volume in the processing tank is around 750ml.

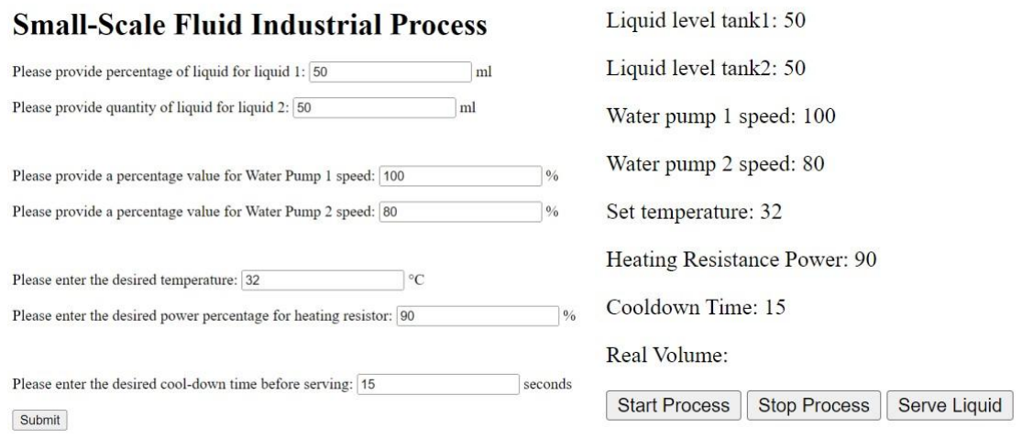
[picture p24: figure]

- Step 3: When the desired liquid volume from storage tank 1 is transferred to the processing tank, water pump 1 stops.

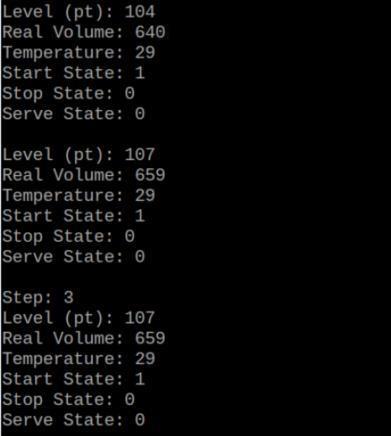
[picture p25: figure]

- Step 4: After water pump 1 stops, the sequential control will go to step 4 as long as all the conditions are met, and water pump 2 starts and will continue to stay ON until the water volume in the processing tank is around 1300ml because the user defined the volume percentage from storage tank 2 as 50% as well.

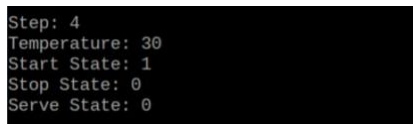
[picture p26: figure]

- Step 5 and 6: Once the volume is reached, water pump 2 is stopped in step 5, and in step 6 the heating resistance is started with the percentage power provided by the user. This resistance will stay on until the desired liquid temperature is reached, in this case, 32°C

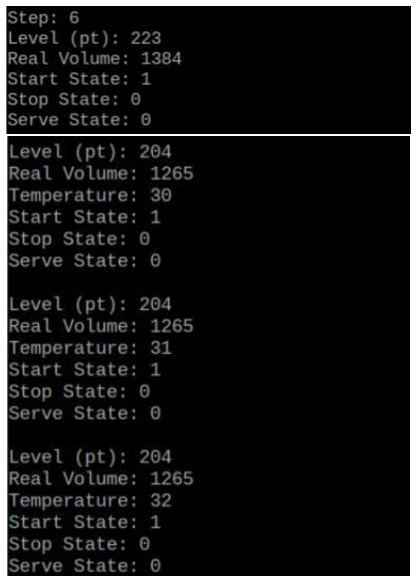
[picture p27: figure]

- Step 7 and 8: In step 7 the heating resistance is turned off, and in step 8, the cooldown counter starts, it will count until 15 in this case. Then, the code will only go to step 8 if the user sends the serve signal.

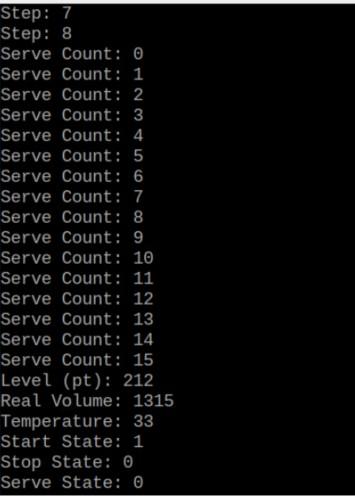
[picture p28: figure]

- Step 9: Here, the electro-valve is opened, and it will reman open until the liquid level is below 100ml.

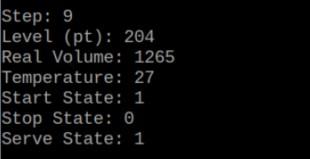
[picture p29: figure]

- Step 10: In step 10, the electro-valve is closed, and the sequential control goes back to step 0

- Calibration:

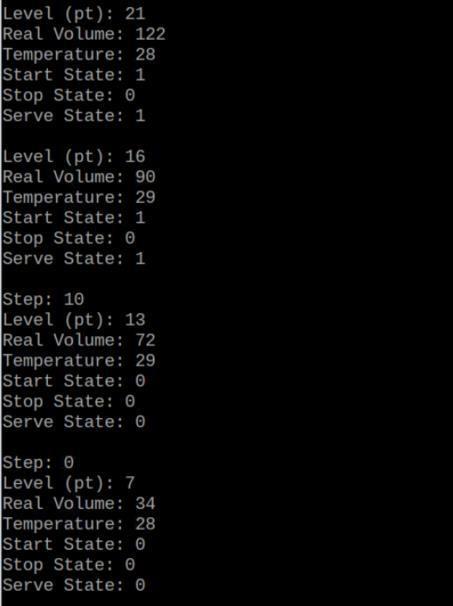
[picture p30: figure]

- To calibrate the pressure sensor, the offset voltage must be set to 1V when the processing tank is empty, and to 4V when the processing tank is full (1300ml). o To calibrate the temperature sensor, the gain must be 5. In other words, for example, if the output of the temperature sensor is 0.23V, the gain potentiometer has to be increased until the output of the OP-AMP is 1.15V.

## 8.0 Troubleshooting

Multiple test points were placed on the PCB to troubleshoot the most important signals:
- As mentioned previously, if temperature readings are erroneous, check the output of the sensor, if it is not around room temperature in millivolts, replace sensor. If the output of the sensor is as expected, check the output of the OP-AMP, if the voltage does not have a gain of 5, calibrate using potentiometer, if you are not getting any gain, replace OP-AMP.
- For the pressure sensor, check the output of the third OP-AMP. When the processing tank is empty, the output of the OP-AMP should be around 1V, if not calibrate using offset potentiometer. Next, fill the tank with 1300ml of water and check the output of the OPAMP, if the output is not around 4V, calibrate using the gain potentiometer. Empty tank and check voltage, it should be around 1V, if not calibrate using offset potentiometer, repeat this process until the output of the OP-AMP is 1V when the tank is empty, and 4V when it is full. If the pressure sensor is not working at all, check the output of the 7810 regulator, if the output is not close to 10V, replace regulator.
- If actuator is not working properly, check the optocoupler’s input voltage, since the signal is inversed, when the actuator is ON, the voltage should be less than 5V, depending on the PWM. If the input of the optocoupler is not close to 0V when the actuator is working close to its maximum power, replace microcontroller because PWM is not working properly. If the input of the optocoupler is the voltage expected, check the drain of MOSFET, it should also be close to 0V, if not, replace MOSFET. Another solution is to check the output of the 24V power supply, if the voltage is not close to 24V, replace power supply.

## Appendix

## A. Illustrations

- PCB: Layout:

## B. Bill of Materials

Quantity | Description
4 | 2.7kΩ RESISTOR
4 | IRFZ44N
4 | 10Ω RESISTOR
4 | 1N5349BG
8 | 1N5401G
4 | 4N25
4 | 330Ω RESISTOR
2 | Water Pumps
1 | Heating Resistance
1 | Electro-valve
2 | HDR1X9
1 | LM7805
13 | 0.1µF CAPACITOR
1 | LM7810
3 | HDR1X3
2 | 0.33µF CAPACITOR
3 | 47kΩ RESISTOR
5 | 10kΩ RESISTOR
1 | 1kΩ POTENTIOMETER
1 | 20kΩ POTENTIOMETER
3 | LMC6062
6 | Capacitive Sensors
1 | 5kΩ POTENTIOMETER
1 | 1kΩ RESISTOR
1 | Logic Level Converter
1 | HDR1X4
2 | ADC0804
2 | 150pF CAPACITOR,
1 | HDR2X5
1 | Microcontroller, ATmega8515
3 | 220Ω RESISTOR
3 | LED
4 | PUSH BUTTON
3 | 390Ω RESISTOR
4 | 100k Ω RESISTOR

## C. Cost Analysis

Component | Quantity | Cost Per Unit | Total
MPX2010 | 1 | $39.35 | $39.35
SEN0508 | 5 | $15.70 | $78.50
LM35DZ Module | 1 | $9.95 | $9.95
AN7805 | 1 | $0.65 | $0.65
AN7810 | 1 | $1.68 | $1.68
ADC0804 | 2 | $8.28 | $16.56
ATmega8515 | 1 | $6.69 | $6.69
Water Pump | 2 | $41.55 | $83.10
Electro Valve | 1 | $13.79 | $13.79
Heating Resistance | 1 | $2.91 | $2.91
MAX232 | 1 | $3.84 | $3.84
½ Vinyl Tube | 1 | $14.95 | $14.95
¼ Vinyl Tube | 1 | $17.25 | $17.25
LMC6062 | 4 | $4.54 | $18.16
4N25 | 5 | $0.92 | $4.60
Total: $311.30

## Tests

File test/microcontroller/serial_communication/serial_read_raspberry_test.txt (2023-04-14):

$serialPort = fopen('/dev/ttyS0', 'r');
system('stty -F /dev/ttyS0 57600');

$a3_received = false;
$b4_received = false;
$c5_received = false;
$d1_received = false;
$e2_received = false;
$f6_received = false;
$n9a_received = false;

while (true) {
    $byte = fread($serialPort, 1);

    switch ($byte) {
        case "\xa3":
            $a3_received = true;
            $b4_received = false;
            $c5_received = false;
            $d1_received = false;
            $e2_received = false;
            $f6_received = false;
            $n9a_received = false;
            break;
        case "\xb4":
            $a3_received = false;
            $b4_received = true;
            $c5_received = false;
            $d1_received = false;
            $e2_received = false;
            $f6_received = false;
            $n9a_received = false;
            break;
        case "\xc5":
            $a3_received = false;
            $b4_received = false;
            $c5_received = true;
            $d1_received = false;
            $e2_received = false;
            $f6_received = false;
            $n9a_received = false;
            break;
        case "\xd1":
            $a3_received = false;
            $b4_received = false;
            $c5_received = false;
            $d1_received = true;
            $e2_received = false;
            $f6_received = false;
            $n9a_received = false;
            break;
        case "\xe2":
            $a3_received = false;
            $b4_received = false;
            $c5_received = false;
            $d1_received = false;
            $e2_received = true;
            $f6_received = false;
            $n9a_received = false;
            break;
        case "\xf6":
            $a3_received = false;
            $b4_received = false;
            $c5_received = false;
            $d1_received = false;
            $e2_received = false;
            $f6_received = true;
            $n9a_received = false;
            break;
        case "\x9a":
            $a3_received = false;
            $b4_received = false;
            $c5_received = false;
            $d1_received = false;
            $e2_received = false;
            $f6_received = false;
            $n9a_received = true;
            break;
        default:
            if ($a3_received) {
                echo "Step: " . ord($byte) . "\n";
                $a3_received = false;
            } elseif ($b4_received) {
                echo "Temperature: " . ord($byte) . "\n";
                $b4_received = false;
            } elseif ($c5_received) {
                $level_pt = ord($byte);
                $real_volume = ($level_pt * 6.24824) - 9.16149;
                echo "Level (pt): " . $level_pt . "\n";
                echo "Real Volume: " . intval($real_volume) . "\n";
                $c5_received = false;
            } elseif ($d1_received) {
                $start_state = ord($byte);
                echo "Start State: " . $start_state . "\n";
                $d1_received = false;
            } elseif ($e2_received) {
                $stop_state = ord($byte);
                echo "Stop State: " . $stop_state . "\n";
                $e2_received = false;
            } elseif ($f6_received) {
                $serve_state = ord($byte);
                echo "Serve State: " . $serve_state . "\n\n";
                $f6_received = false;
            } elseif ($n9a_received) {
                $serve_count = ord($byte);
                echo "Serve Count: " . $serve_count . "\n";
                $n9a_received = false;
            }
			break;
    }
}

fclose($serialPort);

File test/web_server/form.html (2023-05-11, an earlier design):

# Small-Scale Fluid Industrial Process

Please provide percentage of liquid for liquid 1 (30% - 100%): %

Please provide quantity of liquid for liquid 2 (30% - 100%): %

Please provide a percentage value for Water Pump 1 speed (30% - 75%): %

Please provide a percentage value for Water Pump 2 speed (30% - 75%): %

Please enter the desired temperature (23°C - 28°C): °C

Please enter the desired power percentage for heating resistor (95% - 100% is recommended): %

Please enter the desired cool-down time before serving (10s - 120s): seconds

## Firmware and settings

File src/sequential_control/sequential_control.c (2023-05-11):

#include <stdio.h>
#include <stdlib.h>
#include <avr/io.h>
#define F_CPU 8000000UL
#include <util/delay.h>
#include <avr/interrupt.h>
#include <string.h>

//Define constants
#define BAUDRATE 8			//57.6k bps at 8MHz
#define water_p1 OCR1A
#define water_p2 OCR1B
#define h_resis OCR0
#define electro_v PD7

#define CS_ADC_PRESSURE PINC7
#define RD_ADC PINC6
#define WR_ADC PINC5
#define CS_ADC_TEMPERATURE PINC4

#define cap_sen_t1_low PB1
#define cap_sen_t1_high PE1
#define cap_sen_t2_low PC3
#define cap_sen_t2_high PC2
#define cap_sen_pt_high PC1

//Receive Commands
#define com0 0x5B	//Water pump 1 speed percentage 
#define com1 0x4A	//Liquid level tank 1
#define com3 0x3D	//Water pump 2 speed percentage
#define com4 0x2C	//Liquid level tank 2
#define com5 0x1F	//Liquid temperature
#define com6 0x0E	//Waiting time
#define START 0x0A	//Start Indication 
#define STOP 0x5F	//Stop Indication
#define SERVE 0x1B	//Serve Indication 


//Transmit Commands
#define STEP 0xA3				//Step
#define TEMPERATURE 0xB4		//Temperature
#define VOLUME 0xC5				//Volume
#define START_STATE 0xD1		//Start State		
#define STOP_STATE 0xE2			//Stop State
#define SERVE_STATE 0xF6		//Serve State
#define SERVE_COUNT_STATE 0x9A	//Cooldown counter state

//Defines for control panel
#define start_led PB2
#define stop_led PB3
#define serve_led PB4
#define start_signal PD4
#define serve_signal PD6

//Function prototypes
void usart_init(void);
void uart_tx(unsigned char);
unsigned char uart_rx(void);
int ascii_to_numeric(char input[], int);
int numeric_to_percentage_wps(int);
int numeric_to_percentage_h_res(int);
int ascii_input(void);
void pwm_init_p(void);
void pwm_init_r(void);
void electro_v_state(int);

void adc_init(void);
void adc_write_pressure (void);
void adc_write_temperature (void);
void INT_init(void);
int adc_to_temperature(void);
int adc_to_volume(void);
void ISR_INT0_vect(void);
void ISR_INT1_vect(void);
void ISR_INT2_vect(void);
void USART_RX_vect(void);
void control_panel_init(void);

void cap_sensors_init(void);
void uart_transmit(void);
int USART_printCHAR(char character, FILE *stream);
void water_p1_start(int);
void water_p1_stop(int);
void water_p2_start(int);
void water_p2_stop(int);
void stop_actuators(void);

//Global variables
unsigned int step = 0;	
int adc_data_pressure;
int adc_data_temperature;
char RxBuffer[2];
volatile uint8_t RxCounter = 0;
int wp1_speed;
int wp2_speed;
int level_t1;
int level_t2;
int level_pt;
int real_temperature;
int user_temperature;
int hres_power;
int waiting_time;
int start = 0;
int stop = 0;
int serve = 0;
int real_volume;
int volumen_segun_tanque;
int cd_counter;

static FILE mystdout = FDEV_SETUP_STREAM(USART_printCHAR, NULL, _FDEV_SETUP_WRITE);

int main(void)
{
	DDRD |= (1<< electro_v);
	PORTD |= (1 << PD7);			//Initializes valve as OFF.
	
	//Declare variables
	int numeric_value = 0;
	uint16_t percentage = 0;
	int volume;
	float volume_tx;
	
	//Initialize PWM and USART communication
	cli();
	pwm_init_p();
	pwm_init_r();
	usart_init();
	adc_init();
	INT_init();
	cap_sensors_init();
	control_panel_init();
	
	wp1_speed = 0;


	//Local variables
	int wp1_speed_process;
	int wp2_speed_process;
	int volume_product_1;
	int volume_product_2;
	int temperature_process;
	int hres_process;
	int waiting_time_process;

	int cap_sen_t1_low_val;
	int cap_sen_t1_high_val;
	int cap_sen_t2_low_val;
	int cap_sen_t2_high_val;
	int cap_sen_pt_high_val;
	
	int start_signal_value;
	int serve_signal_value;
	
	while (1)
	{
		
		cap_sen_t1_low_val = (PINB & (1 << cap_sen_t1_low)) >> cap_sen_t1_low;
		cap_sen_t1_high_val = (PINE & (1 << cap_sen_t1_high)) >> cap_sen_t1_high;
		cap_sen_t2_low_val = (PINC & (1 << cap_sen_t2_low)) >> cap_sen_t2_low;
		cap_sen_t2_high_val = (PINC & (1 << cap_sen_t2_high)) >> cap_sen_t2_high;
		cap_sen_pt_high_val = (PINC & (1 << cap_sen_pt_high)) >> cap_sen_pt_high;	
		
		adc_write_pressure();		//Trigger Pressure ADC conversion
		volume = adc_to_volume();
		printf("Real volume: %d\n\r", volume);
		_delay_ms(250);
		uart_tx(VOLUME);
		uart_tx(level_pt);
		_delay_ms(10);
		
		adc_write_temperature();
		real_temperature = adc_to_temperature();
		printf("temperature: %d\n\r", real_temperature);
		_delay_ms(250);
		uart_tx(TEMPERATURE);
		uart_tx(real_temperature);
		_delay_ms(10);
		
		//Start Push-button
		start_signal_value = (PIND & (1 << start_signal)) >> start_signal;
		if (start == 0 && start_signal_value == 1 && wp1_speed != 0 && wp2_speed != 0 && level_t1 != 0 && level_t2 != 0 && user_temperature != 0
		&& hres_power != 0 && waiting_time != 0){
			
			PORTB |= (1 << start_led);
			PORTB &= ~(1 << stop_led);
			
			if (step >= 1){			//For stop indication
				step = step - 1;
			}
			_delay_ms(100);
			printf("h");
			stop = 0;
			start = 1;
		}
		
		//Serve Push-button
		serve_signal_value = (PIND & (1 << serve_signal)) >> serve_signal;
		if (serve_signal_value == 1 && step == 8){
			PORTB |= (1 << serve_led);
			serve = 1;
		}
		

		if (start == 0)
		PORTB &= ~(1 << start_led);
		
		if (serve == 0)
		PORTB &= ~(1 << serve_led);
		
		printf("%d\n\r", start);
		_delay_ms(100);
		
		uart_tx(START_STATE);
		uart_tx(start);
		_delay_ms(10);
		
		printf("%d\n\r", stop);
		_delay_ms(100);
		
		uart_tx(STOP_STATE);
		uart_tx(stop);
		_delay_ms(10);
		
		uart_tx(SERVE_STATE);
		uart_tx(serve);
		_delay_ms(10);
		
		
		//T1 error
		if(cap_sen_t1_high_val == 0 && cap_sen_t1_low_val == 1){
			stop_actuators();
			//printf("Error t1\n\r");
		}
		
		//T1 is empty
		if(cap_sen_t1_high_val == 1 && cap_sen_t1_low_val == 1){
			stop_actuators();
			stop = 1;
			start = 0;
			//printf("T1 empty\n\r");
		}
		
		//T2 error
		if(cap_sen_t2_high_val == 0 && cap_sen_t2_low_val == 1){
			stop_actuators();
			stop = 1;
			start = 0;
			//printf("Error t2\n\r");
		}
		
		//T2 is empty
		if(cap_sen_t2_high_val == 1 && cap_sen_t2_low_val == 1){
			stop_actuators();
			stop = 1;
			start = 0;
			//printf("T2 empty\n\r");
		}
		
		
		
		
		//---------------------Sequential Control---------------------
		
		//Step 0
		//Waits for serial values from Raspberry Pi
		if(step == 0){
			printf("Step: %d\n\r", step);
			_delay_ms(100);
			
			uart_tx(STEP);
			uart_tx(step);
			_delay_ms(10);		
			}

		//Step1
		//Transfers serial variables to process values
		if(step == 0 && start == 1 && stop == 0){ 
			
			step = 1;
			printf("Step: %d\n\r", step);
			_delay_ms(500);
			
			uart_tx(STEP);
			uart_tx(step);
			_delay_ms(10);
			
			//Transfer communication variables to process variables
			wp1_speed_process = wp1_speed;
			printf("WP1 speed: %d\n\r", wp1_speed_process);
			
			wp2_speed_process = wp2_speed;
			printf("WP2 speed: %d\n\r", wp2_speed_process);
			
			volume_product_1 = level_t1 * 13;
			printf("volume product 1: %d\n\r", volume_product_1);
			
			volume_product_2 = level_t2 * 13;
			printf("volume product 2: %d\n\r", volume_product_2);
			
			temperature_process = user_temperature;
			printf("temperature: %d\n\r", temperature_process);
			
			hres_process = hres_power;
			printf("Heating Resistance Power: %d\n\r", hres_process);
			
			waiting_time_process = waiting_time;
			printf("waiting time: %d\n\r", waiting_time_process);
		}
		
		//Step 2
		//Starts Water Pump 1
		if(step == 1 && start == 1 && stop == 0 && cap_sen_t1_low_val == 0 && real_volume <= 100){
			
			step = 2;
			printf("Step: %d\n\r", step);
			_delay_ms(500);
			
			uart_tx(STEP);
			uart_tx(step);
			_delay_ms(10);
			
			percentage = numeric_to_percentage_wps(wp1_speed_process);
			water_p1_start(percentage);	
		}
		
		//Step 3
		//Stops Water Pump 1
		if(step == 2 && start == 1 && stop == 0 && cap_sen_t1_low_val == 0 && real_volume >= volume_product_1){
			
			step = 3;
			printf("Step: %d\n\r", step);
			_delay_ms(500);
			
			uart_tx(STEP);
			uart_tx(step);
			_delay_ms(10);
			
			percentage = numeric_to_percentage_wps(wp1_speed_process);
			water_p1_stop(percentage);
		}
		
		//Step 4
		//Starts Water Pump 2
		if(step == 3 && start == 1 && stop == 0 && cap_sen_t2_low_val == 0 && real_volume >= volume_product_1){
				
			step = 4;
			printf("Step: %d\n\r", step);
			_delay_ms(500);
			
			uart_tx(STEP);
			uart_tx(step);
			_delay_ms(10);
			
			percentage = numeric_to_percentage_wps(wp2_speed_process);
			water_p2_start(percentage);	
		}
		
		//Step 5
		//Stop Water Pump 2
		if(step == 4 && start == 1 && stop == 0 && cap_sen_t2_low_val == 0 && real_volume >= (volume_product_1 + volume_product_2)){
			
			step = 5;
			printf("Step: %d\n\r", step);
			_delay_ms(500);
			
			/*uart_tx(STEP);
			uart_tx(step);
			_delay_ms(10);*/
			
			percentage = numeric_to_percentage_wps(wp2_speed_process);
			water_p2_stop(percentage);	
		}
		
		//Step 6
		//Start Heating Resistance
		if(step == 5 && start == 1 && stop == 0 &&  real_temperature <= temperature_process){
			
			step = 6;
			printf("Step: %d\n\r", step);
			_delay_ms(100);
			
			uart_tx(STEP);
			uart_tx(step);
			_delay_ms(10);
			
			percentage = numeric_to_percentage_h_res(hres_process);
			h_resis = percentage;
		}
		
		//Step 7
		//Stop Heating Resistance
		if(step == 6 && start == 1 && stop == 0 &&  real_temperature >= temperature_process){
			
			step = 7;
			printf("Step: %d\n\r", step);
			_delay_ms(500);
			
			uart_tx(STEP);
			uart_tx(step);
			_delay_ms(10);
			
			h_resis = 0;
		}
		
		//Step 8
		//Cooldown timer
		if(step == 7 && start == 1 && stop == 0){
			
			step = 8;
			printf("Step: %d\n\r", step);
			_delay_ms(500);
			
			uart_tx(STEP);
			uart_tx(step);
			_delay_ms(10);
			
			for(cd_counter = 0; cd_counter <= waiting_time_process; cd_counter++){
				_delay_ms(1000);
				printf("%d\n\r", cd_counter);
				
				/*uart_tx(SERVE_COUNT_STATE);
				uart_tx(cd_counter);
				_delay_ms(10);*/
				
				
				if(stop == 1)
				break;
			}
			//printf("Time Completed\n\r");
		}
		
		//Step 9
		//Liquid Serving
		if(step == 8 && start == 1 && stop == 0 && serve == 1){
			step = 9;
			PORTB |= (1 << serve_led);
			printf("Step: %d\n\r", step);
			_delay_ms(500);
			
			uart_tx(STEP);
			uart_tx(step);
			_delay_ms(10);
			
			electro_v_state(1);	
		}
		
		//Step 10
		//Close electro-valve
		if(step == 9 && start == 1 && stop == 0 && real_volume <= 100){
			
			step = 10;
			printf("Step: %d\n\r", step);
			_delay_ms(500);
			
			uart_tx(STEP);
			uart_tx(step);
			_delay_ms(10);
			
			electro_v_state(0);
			//printf("Process Completed\n\r");
			
			serve = 0;
			start = 0;
			step = 0;	
		}
		
	}
	return 0;
}

//-----------------------------------------------------------------------------------------
//-------------------------------------Functions-------------------------------------------

//Initializes USART
void usart_init (void){
	UBRRL=BAUDRATE;								//sets baud rate
	UCSRB|=(1<<TXEN)|(1<<RXEN)|(1<<RXCIE);					//enables receiver and transmitter
	UCSRC|=(1<<URSEL)|(1<<UCSZ0)|(1<<UCSZ1);	// 8bit data format
	 stdout = &mystdout;
}

//Transmits data to USART
void uart_tx (unsigned char data){
	while (!(UCSRA & (1<<UDRE)));           // bit mask to check if UDRE bit is set
	UDR = data;
}

int USART_printCHAR(char character, FILE *stream)
{
	uart_tx(character);
	return 0;
}

//Receive data from USART
unsigned char uart_rx(void){
	while (!(UCSRA & (1<<RXC)));          //Bit mask to check if RXC bit is set
	return UDR;
}

//Initializes PWM for controlling water pump speed
void pwm_init_p(void){
	DDRD |= (1 << PD5);  		// Set PD5 (OC1A) as output pin
	DDRE |= (1 << PE2);  		//Set PE2 (OC1B) as output pin

	// Set Timer/Counter1 in Fast PWM mode, with non-inverted PWM output on OC1A
	TCCR1A |= (1 << COM1A1) | (1 << COM1A0) | (1 << COM1B1) | (1 << COM1B0) | (1 << WGM11) | (1 << WGM10);	//COM1A0 Inverts the signal
	TCCR1B |= (1 << WGM12) | (1 << CS10); 	// Set the prescaler value to no prescaling
}

//Initializes PWM for controlling heater resistor
void pwm_init_r(){
	DDRB |= (1 << PB0);  // Set PB0 (OC0) as output pin
	TCCR0 |= (1 << COM01) | (1 << COM00) | (1 << WGM01) | (1 << WGM00);
	TCCR0 |= (1 << CS00);
}

void control_panel_init(void){
	DDRB |= (1 << start_led);
	DDRB |= (1 << stop_led);
	DDRB |= (1 << serve_led);
	
	DDRD &= ~(1 << start_signal);
	DDRD &= ~(1 << serve_signal);
}

//Convert ASCII input to numeric value
int ascii_to_numeric(char input[], int length){
	int value = 0;
	for (int i = 0; i < length; i++) {
		value = value * 10 + (input[i] - '0');
	}
	return value;
}

// Convert numeric value to percentage for water pumps
int numeric_to_percentage_wps(int numeric_value ){
	int percentage = 0;
	percentage = (uint16_t)((uint32_t)numeric_value * 1023 / 100) & 0xFFFF;
	return percentage;
}

// Convert numeric value to PWM duty cycle percentage for heater resistor
int numeric_to_percentage_h_res(int numeric_value ){
	int percentage = 0;
	percentage = (numeric_value * 255) / 100;
	return percentage;
}

//Sets the state of valve based on the received numeric value
void electro_v_state(int numeric_value){
	if(numeric_value == 1)
	PORTD &= ~(1 << PD7);
	else
	PORTD |= (1 << PD7);
}

// Read input from USART and return numeric value
int ascii_input(void){
	char input[3];
	int numeric_value = 0;
	uint16_t percentage = 0;
	int length = 0;
	
	do{
		input[length] = uart_rx();
		uart_tx(input[length]);
		length++;
	} while ((length < 4) && (input[length-1] != '\r'));
	
	numeric_value = ascii_to_numeric(input, length-1);

	return numeric_value;
}

//Starts Water Pump 1
void water_p1_start(int max){
	int m;
	for(m = 0; m <= max; m++){
		water_p1 = m;
		_delay_ms(3);				//Ensures that the loop completes within 4 seconds.
		if(stop == 1)
			break;	
	}
}

//Stops Water Pump 1
void water_p1_stop(int max){
	int s;
	for(s = max; s >= 0; s--){
		water_p1 = s;
		_delay_ms(3);				//Ensures that the loop completes within 3 seconds.
		if(stop == 1)
			break;
	}
}

//Starts Water Pump 2
void water_p2_start(int max){
	int m;
	for(m = 0; m <= max; m++){
		water_p2 = m;
		_delay_ms(3);				//Ensures that the loop completes within 4 seconds.
		if(stop == 1)
			break;		
	}
}

//Stops Water Pump 2
void water_p2_stop(int max){
	int s;
	for(s = max; s >= 0; s--){
		water_p2 = s;
		_delay_ms(3);				//Ensures that the loop completes within 3 seconds.
		if(stop == 1)
			break;
	}	
}

//-------------------------------------------------------------------
//-------------------------------------------------------------------

//Initializes ADC control pins and set input/output pins
void adc_init(void){
	DDRC |= (1 << CS_ADC_PRESSURE);
	DDRC |= (1 << CS_ADC_TEMPERATURE);
	DDRC |= (1 << RD_ADC);
	DDRC |= (1 << WR_ADC);
	DDRA = 0x0;
	
	PORTC |= (1 << CS_ADC_PRESSURE);
	PORTC |= (1 << CS_ADC_TEMPERATURE);
	PORTC |= (1 << RD_ADC);
	PORTC |= (1 <<  WR_ADC);
}

//Triggers ADC conversion
void adc_write_pressure(void){
	//Writing Cycle
	PORTC &= ~(1 << CS_ADC_PRESSURE);
	PORTC &= ~(1 << WR_ADC);
	PORTC |= (1 <<  WR_ADC);
	PORTC |= (1 << CS_ADC_PRESSURE);
}

//Interrupt service routine for reading  pressure ADC data
ISR(INT0_vect)
{
	PORTC |= (1 << CS_ADC_TEMPERATURE);
	
	//Reading Cycle
	PORTC &= ~(1 << CS_ADC_PRESSURE);
	_delay_us(1);
	PORTC &= ~(1 << RD_ADC);
	_delay_us(1);
	adc_data_pressure = PINA;
	PORTC |= (1 << RD_ADC);
	_delay_us(1);
	PORTC |= (1 << CS_ADC_PRESSURE);
	_delay_us(1);
	
	//usart_tx(adc_data_pressure);
}

void adc_write_temperature(void){
	//Writing Cycle
	PORTC &= ~(1 << CS_ADC_TEMPERATURE);
	PORTC &= ~(1 << WR_ADC);
	PORTC |= (1 <<  WR_ADC);
	PORTC |= (1 << CS_ADC_TEMPERATURE);
}

//Interrupt service routine for reading  temperature ADC data
ISR(INT1_vect) {
	PORTC |= (1 << CS_ADC_PRESSURE);
	
	//Reading Cycle
	PORTC &= ~(1 << CS_ADC_TEMPERATURE);
	_delay_us(1);
	PORTC &= ~(1 << RD_ADC);
	_delay_us(1);
	adc_data_temperature = PINA;
	PORTC |= (1 << RD_ADC);
	_delay_us(1);
	PORTC |= (1 << CS_ADC_TEMPERATURE);
	_delay_us(1);
	
	//usart_tx(adc_data_temperature);
}

//Configures interrupts 
void INT_init(void){
	// Sets up INT0 and INT1 to trigger on falling edge
	MCUCR |= (1 << ISC01) | (1 << ISC11);
	MCUCR &= ~(1 << ISC00) & ~(1 << ISC10);
	EMCUCR |= (1 << ISC2);
	
	GICR |= (1 << INT0) | (1 << INT1) | (1 << INT2);	//Enable INT0 and INT1 interrupts
	sei();												//Enable global interrupts
}

//Converts ADC data into temperature
int adc_to_temperature(void){
	int temperature_adc;
	temperature_adc =(int)((adc_data_temperature - 2) * 100) / 255;			//2 is for fine tuning
	return (int)temperature_adc;
}

//Calculates liquid level in millimiters and real volume 
int adc_to_volume(void){
	float adc_value;
	
	adc_value = ((float)adc_data_pressure * 0.0196078)  ;					//Converts back to range of voltage 0-5V
	
	level_pt = (adc_value - 1) * 78.6;										//Liquid level in millimeters 
	printf("level in mm: %d\n\r", level_pt);

	real_volume = (level_pt * 6.24824) - 9.16149;
	
	return (int)real_volume;
}

//-------------------------------------------------------------------
//-------------------------------------------------------------------

void cap_sensors_init(void){
	DDRE &= ~(1 << cap_sen_t1_low) & ~(1 << cap_sen_t1_high);
	DDRC &= ~(1 << cap_sen_t2_low) & ~(1 << cap_sen_t2_high) & ~(1 << cap_sen_pt_high);
}

//Reads incoming data bytes from serial port
ISR(USART_RX_vect){
	
	//Read incoming byte and store it in buffer
	while (RxCounter < 2){
		if (UCSRA & (1 << RXC)) {		// Check if there is data available
			RxBuffer[RxCounter] = UDR;
			RxCounter++;
		}
	}
	
		//Water pump 1 received speed data
		if (RxBuffer[0] == 0x5B){	
			wp1_speed = RxBuffer[1];
			printf("WP1 Speed: %d\n\r", wp1_speed);
		}
		
		//Tank 1 volume data
		else if (RxBuffer[0] == 0x4A){			
			level_t1 = RxBuffer[1];
			printf("Tank 1 Volume: %d\n\r", level_t1);
		}
	
		//Water pump 2 received speed data
		else if (RxBuffer[0] == 0x3D){			
			wp2_speed = RxBuffer[1];
			printf("WP2 Speed: %d\n\r", wp2_speed);
		}
	
		//Tank 2 volume data
		else if (RxBuffer[0] == 0x2C){			
			level_t2 = RxBuffer[1];
			printf("Tank 2 Volume: %d\n\r", level_t2);
		}
			
		//Liquid's temperature data
		else if (RxBuffer[0] == 0x1F){	
			user_temperature = RxBuffer[1];
			printf("Liquid's Temperature: %d\n\r", user_temperature);
		}
		
		else if (RxBuffer[0] == 0x4E){
			hres_power = RxBuffer[1];
			//printf("Heating Resistance Power: %d\n\r",hres_power);
		}
		
		//Cooldown timer data
		else if (RxBuffer[0] == 0x0E){		
			waiting_time = RxBuffer[1];
			printf("Waiting time: %d\n\r", waiting_time);
		}
		
		//Start signal
		else if (RxBuffer[0] == START){	
			
			if (wp1_speed != 0 && wp2_speed != 0 && level_t1 != 0 && level_t2 != 0 && user_temperature != 0
			&& hres_power != 0 && waiting_time != 0){
				
				PORTB |= (1 << start_led);
				PORTB &= ~(1 << stop_led);
				
				if (step >= 1 && start == 0){	//For stop indication
					step = step - 1;
				}
				
				start = RxBuffer[1];
				stop = 0;
			}
		}
		
		else if (RxBuffer[0] == STOP){			
			stop = RxBuffer[1];
			printf("Indication: STOP %d\n\r", stop);
			stop_actuators();
		}
		
		else if (RxBuffer[0] == SERVE){			
			serve = RxBuffer[1];
		}
			
		RxCounter = 0;
		memset(RxBuffer, 0, sizeof(RxBuffer));
}

//Stops all actuators
void stop_actuators(void){
			
			PORTB |= (1 << stop_led);
			PORTB &= ~(1 << start_led);
			PORTB &= ~(1 << serve_led);
			
			stop = 1;
			start = 0;
			water_p1 = 0;	
			water_p2 = 0;
			h_resis = 0;
			PORTD |= (1 << electro_v);	
}

//Stop button service interrupt function
ISR(INT2_vect){
	_delay_ms(100);
	stop = 1;
	stop_actuators();
	start = 0;
}

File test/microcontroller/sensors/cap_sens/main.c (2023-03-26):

#include <avr/io.h>
#include <stdio.h>
#include <stdlib.h>
#define F_CPU 8000000L
#include <util/delay.h>

#define BAUDRATE 8

#define cap_sen_t1_low PE0
#define cap_sen_t1_high PE1
#define cap_sen_t2_low PC3
#define cap_sen_t2_high PC2
#define cap_sen_pt_high PC1

void usart_init(void);
void usart_tx(unsigned char);

void cap_sensors_init(void);

int main (void)
{
	usart_init();
	cap_sensors_init();

	int cap_sen_t1_low_val = 0;
	int cap_sen_t1_high_val = 0;
	int cap_sen_t2_low_val = 0;
	int cap_sen_t2_high_val = 0;
	int cap_sen_pt_high_val = 0;

	while(1){
		cap_sen_t1_low_val = (PINE & (1 << cap_sen_t1_low)) >> cap_sen_t1_low;
		_delay_ms(100);
		usart_tx(cap_sen_t1_low_val);
		
		/*_delay_ms(1000);
		
		cap_sen_t1_high_val = (PINE & (1 << cap_sen_t1_high)) >> cap_sen_t1_high;
		_delay_ms(100);
		usart_tx(cap_sen_t1_high_val);
		
		_delay_ms(1000);
		
		cap_sen_t2_low_val = (PINC & (1 << cap_sen_t2_low)) >> cap_sen_t2_low;
		_delay_ms(100);
		usart_tx(cap_sen_t2_low_val);
		
		_delay_ms(1000);
		
		cap_sen_t2_high_val = (PINC & (1 << cap_sen_t2_high)) >> cap_sen_t2_high;
		_delay_ms(100);
		usart_tx(cap_sen_t2_high_val);
		
		_delay_ms(1000);
		
		cap_sen_pt_high_val = (PINC & (1 << cap_sen_pt_high)) >> cap_sen_pt_high;
		_delay_ms(100);
		usart_tx(cap_sen_pt_high_val);
		
		_delay_ms(1000);*/
		
	}
	return 0;
}

void usart_init (void){
	UBRRL=BAUDRATE;
	UCSRB|=(1<<TXEN)|(1<<RXEN);
	UCSRC|=(1<<URSEL)|(1<<UCSZ0)|(1<<UCSZ1);
}

void usart_tx (unsigned char data){
	while (!( UCSRA & (1<<UDRE)));
	UDR = data;
}


void cap_sensors_init(void){
	DDRE &= ~(1 << cap_sen_t1_low) & ~(1 << cap_sen_t1_high);
	DDRC &= ~(1 << cap_sen_t2_low) & ~(1 << cap_sen_t2_high) & ~(1 << cap_sen_pt_high);
	
	return 0;
}

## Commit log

2023-03-15 v5.0
    Working code for serial input of 3 ASCII characters that represent percentage (0-100) and outputs corresponding value for duty cycle. Works for 1 water pump.
2023-03-15 Revert "v5.0"
    This reverts commit 2a0c7322cbe95bdac00d333153f2bb5ef989f5ff.
    [main.c]
2023-03-15 v4.0
    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
2023-03-16 v5
    Working code for serial input of 3 ASCII characters that represent percentage (0-100) and outputs corresponding value for duty cycle. Works for 2 water pumps.
2023-03-16 v5.1
    Working code for serial input of 3 ASCII characters that represent percentage (0-100) and outputs corresponding value for duty cycle. Works for 2 water pumps, and 1 heating resistor.
2023-03-17 v1
    Working code for serial input of 3 ASCII characters that represent percentage (0-100) and outputs corresponding value for duty cycle for 2 water pumps and 1 heating resistance. Also reads ASCII input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
2023-03-17 v4.0
    Working code for 1 ADC. Data bus is connected to PORTA, and control signals are connected to PORTE.
2023-03-17 v4.1
    Changed ADC control pins from PORTE to PORTC
2023-03-18 v5
    Added second adc for temperature.
2023-03-19 v5.3
    Converts ADC temperature reading to numeric value and displays temperature in degree Celsius. Does not work well with pressure sensor yet.
    [main.c]
2023-04-07 v2
    Sequential control is working, but minor errors with printf functions
    [main.c]
2023-04-10 Update main.c
    Works with error conditions of tanks
    [main.c]
2024-06-17 Structure modification v1.5
    [control_panel - Board Outline.gbr, control_panel - Copper Bottom.gbr, control_panel - Copper Top-Copper Bottom.drl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]
